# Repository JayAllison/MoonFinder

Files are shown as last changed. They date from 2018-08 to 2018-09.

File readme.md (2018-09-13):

Can I aim a telescope with a Raspberry Pi, some stepper motors, and some open-source software? Let's try!

Can I use **ALL** of the GPIO pins or a Raspberry Pi? Let's try!

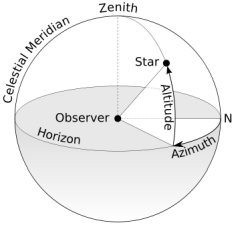
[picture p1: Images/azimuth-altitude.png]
Azimuth & Altitude
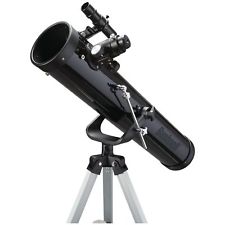
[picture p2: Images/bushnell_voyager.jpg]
 

### Equipment:

* Bushnell Voyager basic telescope (700mm x 76mm)
    * Probably need a mock-up, too - make it from 4" PVC?
* Raspberry Pi (I have both a Zero W and a 3B+, so I need to determine how much horsepower this application needs)
    * I also have protoboards to fit the GPIO of both
* 28BYJ-48 stepper motors and LN2003 drivers (I think I only need two, but I ordered [this five-pack](https://smile.amazon.com/gp/product/B015RQ97W8/) from Amazon)
* LSM303 digital compass (I ordered [this dev board](https://www.adafruit.com/product/1120) from Adafruit)
* Display (I ordered [this TFT display](https://smile.amazon.com/gp/product/B07B4BDWCL/) from Amazon)
    * I can always fall back to [this OLED display](https://smile.amazon.com/gp/product/B00O2LLT30/) if needed
* Limit switches (I ordered [this ten-pack](https://smile.amazon.com/gp/product/B00MFRMFS6/) from Amazon)
* 3/4" fender washers to use as weights (got two 25-packs at Home Depot)
* ~~Telephone handset jacks and cables for connecting motors to control board (ordered from Amazon)~~
* A two-way level (I ordered [this one](https://smile.amazon.com/gp/product/B000EDSSDO/) from Amazon)
* Buttons for user input (I ordered [this pack](https://smile.amazon.com/gp/product/B07CGCPGPT/) from Amazon)
* GPS (I ordered [this unit](https://smile.amazon.com/gp/product/B01H5FNA4K/) from Amazon)

### Source Code:

* My repository: https://github.com/JayAllison/MoonFinder

### Tools:

* Fritzing: http://fritzing.org/home/

### References:

* Python Raspberry Pi GPIO Wrapper Library: https://gpiozero.readthedocs.io/
* Raspberry Pi GPIO Pinout: https://pinout.xyz/
* Stepper motor control with RPi: https://tutorials-raspberrypi.com/how-to-control-a-stepper-motor-with-raspberry-pi-and-l293d-uln2003a/
    * But, my BlindsBot project ended up being a better reference for the step sequence
* LSM303 reading with RPi: https://github.com/adafruit/Adafruit_Python_LSM303/tree/master/examples
* ST7735 Display Library: https://github.com/cskau/Python_ST7735
    * I got the cheap Amazon display I purchased working with the examples using the connections listed below
    * The examples are written for a 160x128 display, this one is 128x128
* Python Image Library fork (pillow): https://pillow.readthedocs.io/en/5.2.x/
* U-Blox U-Center, Windows software for GPS module: https://www.u-blox.com/en/product/u-center-windows
* Serial Port driver: https://pythonhosted.org/pyserial/
* NMEA sentence information: http://aprs.gids.nl/nmea/
* RPi serial port info, per model: https://www.raspberrypi.org/documentation/configuration/uart.md
* gpsd, gpsmon: https://www.rs-online.com/designspark/add-gps-time-and-location-to-a-raspberry-pi-project
    * don't set gpsd to start up automatically or it will monopolize the serial port
* Astronomical positioning library: http://rhodesmill.org/pyephem/
* Python version of World Magnetic Model (offline): https://pypi.org/project/geomag/
* OpenSCAD (parametric 3D modeling): http://www.openscad.org/cheatsheet/

### 3D Models:

* need to design a pan-and-tilt mount for the telescope
* Do I need a counter-balance?
* Do I want to gear down the movement? or use worm gears instead?
* Can I do something kind of like this "Dobsonian" telescope?

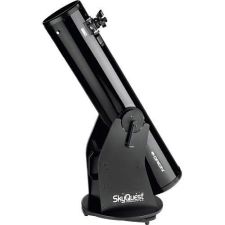
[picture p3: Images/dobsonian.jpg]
Dobsonian Telescope


### Basic Approach:

* User sets up telescope and verifies that the base is level
* Use compass to orient rotation (azimuth) of telescope to true North
* Use limit switch to orient angle (altitude) of telescope to horizontal
* Use library to calculate apparent position (azimuth, altitude) of desired celestial object
* Use stepper motors to aim telescope to that position
* Use stepper motors to either:
    * hold position
    * track object

### Remaining questions:

* How will the user specify the lat/lon location and altitude?
* How will the user select the celestial object?
* Will all of the libraries work offline, or will an internet connection be required?
* How to determine true north vs magnetic north, based on location?
* How to convert "apparent position" (azimuth, altitude) to pan and tilt rotations?
* How to implement tracking? How smooth do I want it to be?

### Hardware Ideas:

* I2C OLED screen or something similar
* Buttons for inputs (D Pad, 5 button style, etc)?
* Button for screen brightness?

### Software Ideas:

Display a list of known celestial objects that are currently visible?

### Raspberry Pi Setup Tasks:

*These are my standard steps for setting up a secure, headless Raspberry Pi*

- [x] Install Raspbian on RPi0W, add to WiFi, install updates
- [x] Change RPi hostname
- [x] Change locale via raspi-config? No, the new Raspbian setup took care of this.
- [x] Change keyboard layout via raspi-config? Yes, the new Raspbian setup did not take care of this.
- [x] Change timezone via raspi-config? No, the new Raspbian setup took care of this.
- [x] Enable SSH via raspi-config
- [x] Set up key-based SSH authentication
    * http://raspi.tv/2012/how-to-set-up-keys-and-disable-password-login-for-ssh-on-your-raspberry-pi
    * create sshd banner
- [x] Set up IP address emailing (had to use nano -u to remove dos line endings after I scp'd the file over from my PC)
    * https://gist.github.com/Morrolan/2987424#file-check_ip-py 
- [x] Install git? No, it was already installed. (Don't forget to set name and email address, though.)
- [x] Install screen
- [x] Install ipython
- [x] Modify /etc/nanorc to my liking
- [x] Set up RPi to boot w/o GUI via raspi-config
- [x] Set up RPi /etc/wpa_supplicant/wpa_supplicant.conf with WiFi credentials for home & work

### TFT Display Connections:

Display|Raspberry Pi
---|---
5V|any RPi 5V
GND|any RPi GND
GND|NC
NC|NC
NC|NC
LED|I connected this to RPi 3.3V
SCL|RPi SCLK
SDA|RPi MOSI
RS|GPIO 24 (per the example)
RST|GPIO 25 (per the example)
CS|RPi CE0

### Raspberry Pi Header Pin Allocation:

Usage|Pin|Name| |Name|Pin|Usage
----|---|---|---|---|---|---
X|_1_|**3.3V**| |**5V**|2|X
COMPASS|_3_|**I2C SDA (GPIO2)**| |**5V**|_4_|X
COMPASS|_5_|**I2C SCL (GPIO3)**| |**GND**|_6_|X
ERROR_LED|_7_|**GPIO4**| |**(GPIO14) TXD**|_8_|GPS
X|_9_|**GND**| |**(GPIO15) RXD**|_10_|GPS
MOTOR 1|_11_|**GPIO17**| |**(GPIO18) PWM0**|_12_|DISPLAY?
MOTOR 1|_13_|**GPIO27**| |**GND**|_14_|X
MOTOR 1|_15_|**GPIO22**| |**GPIO23**|_16_|MOTOR 1
X|_17_|**3.3V**| |**GPIO24**|_18_|DISPLAY
DISPLAY|_19_|**SPI MOSI (GPIO10)**| |**GND**|_20_|X
DISPLAY|_21_|**SPI MISO (GPIO9)**| |**GPIO25**|_22_|DISPLAY
DISPLAY|_23_|**SPI CLK (GPIO11)**| |**(GPIO8) SPI CE0**|_24_|DISPLAY
X|_25_|G**ND**| |**(GPIO7) SPI CE1**|_26_|SW 1
RESERVED|_27_|**ID_SD**| |**ID_SC**|_28_|RESERVED
MOTOR 2|_29_|**GPIO5**| |**GND**|_30_|X
MOTOR 2|_31_|**GPIO6**| |**GPIO12**|_32_|SW 2
LIMIT SWITCH|_33_|**PWM1 (GPIO13)**| |**GND**|_34_|X
MOTOR 2|_35_|**GPIO19**| |**GPIO16**|_36_|SW 3
MOTOR 2|_37_|**GPIO26**| |**GPIO20**|_38_|SW 4
X|_39_|**GND**| |**GPIO21**|_40_|SW 5

### Wiring to Handset:

* Using two stranded Ethernet cables

Wire|Cable A
---|---
1|5V
2|Display SPI MOSI
3|Display SPI MISO
4|Display SPI CLK
5|Display SPI CS
6|Display RS
7|Display RST
8|Display Backlight PWM

Wire|Cable B
---|---
1|3.3V
2|SW 1
3|SW 2
4|SW 3
5|SW 4
6|SW 5
7|ERROR LED
8|N/C

### Project Tasks:

- [x] Create ssh key for Bitbucket
- [x] Check out moonfinder repository onto RPi
- [x] Write pyephem example to show myself I can do it
- [x] Write stepper example to show myself I can do it
- [x] Enable I2C via raspi-config
- [x] Write compass example to show myself I can do it
- [x] Enable SPI via raspi-config
- [x] Write display example to show myself I can do it
- [x] Disable serial console, enable serial hardware via raspi-config, then reboot
- [x] Write GPS example to show myself I can do it
- [x] Install gpsd & gpsmon (only run gpsd on boot if you want to lose control of serial0!)
- [ ] Work on prototype of pan & tilt bracket
- [x] Build handset prototype
- [x] Design menuing software
- [ ] *Task TBD*
- [ ] *Task TBD*
- [ ] *Task TBD*
- [ ] *Task TBD*
- [ ] *Task TBD*
- [ ] *Task TBD*
- [ ] *Task TBD*
- [ ] Put it all together and try it out!

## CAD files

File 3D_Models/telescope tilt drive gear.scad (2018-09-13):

// Lay out the gears that I am going to use for the telescope mount

// the gear library I'm using
use <parametric_involute_gear_v5.0.scad>;

// my explicit gear parameters
number_of_teeth = 20;
pitch_diameter = 30;
pressure_angle = 30;
border_width = 5;
gear_thickness = 8;
border_thickness = gear_thickness;
hub_thickness = 13;
hub_diameter = 12;
circles = 0;

// my derived gear parameters
diametral_pitch = number_of_teeth / pitch_diameter;
echo(str("Diametral Pitch = ", diametral_pitch));
rim_thickness = border_thickness;
rim_width = border_width;

// gear parameters I'm not using
clearance = 0;
bore_diameter = 0;
backlash = 0;

// assemble the big gear - remember that its diametral pitch must match the mating gear
difference() {
    // lay out the basic gear
    gear(
        number_of_teeth=number_of_teeth,
        diametral_pitch=diametral_pitch,
        pressure_angle=pressure_angle,
        clearance=clearance,
        gear_thickness=gear_thickness,
        rim_thickness=rim_thickness,
        rim_width=rim_width,
        hub_thickness=hub_thickness,
        hub_diameter=hub_diameter,
        bore_diameter=bore_diameter,
        circles=circles,
        backlash=backlash
    );
    // create the axis type that I expect
    cube([5, 3, hub_thickness*2], center=true);
}

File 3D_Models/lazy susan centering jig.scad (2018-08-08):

// create a jig that fits in the center of the lazy susan bearing and aligns the bearing with the pin hole

hole_diameter = 33;
hole_height = 8;

pin_diameter = 3;
pin_height = 5;

union() {
    cylinder(h=hole_height, d=hole_diameter, center=false, $fn=256);
    translate([0,0,hole_height])
        cylinder(h=pin_height, d=pin_diameter, center=false, $fn=256);
}

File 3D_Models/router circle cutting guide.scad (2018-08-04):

// a custom jig for my Rigid router to cut a circle of the specified diameter
// this jig connects into the attachment rod holes that are built into my router's base

// specified parameter - how big of a circle do I want to cut: 8" ~= 203 mm
cut_circle_diameter = 205;

// specified parameter - what size bit am I using: 3/8" ~= 9.5 mm
bit_diameter = 10;

// measurements of my router
rod_depth = 20;
rod_width = 5;
rod_spread = 60;
bit_to_rod_bar_spacing = 65;

// design measurements for the jig
pin_diameter = 4;
disc_height = 18;
shaft_width = 10;
stiffener_height = 3;
stiffener_width = 0.4*3;

// calculated parameters
disc_diameter = pin_diameter*3;
shaft_length = cut_circle_diameter/2 + bit_diameter/2 - bit_to_rod_bar_spacing;
rod_spread_bar_length = rod_spread + rod_width;
shaft_height = shaft_width/2;

// put it all together
union() {
    difference() {
        union() {
            // create the pivot disc
            cylinder(h=disc_height, d=disc_diameter, center=true, $fn=256);
            // attach the extension shaft
            translate([-shaft_length, -shaft_width/2, -disc_height/2])
                cube(size=[shaft_length, shaft_width, shaft_height]);
            // add a stiffening spine to the extension shaft
            translate([-shaft_length, -stiffener_width/2, -disc_height/2+shaft_height])
                cube(size=[shaft_length, stiffener_width, stiffener_height]);
        }
        // punch the pin hole through the pivot disc
        cylinder(h=disc_height*2, d=pin_diameter, center=true, $fn=256);
    }
    // attach the rod spread bar to the shaft
    translate([-shaft_length, -rod_spread_bar_length/2, -disc_height/2]) {
        cube(size=[shaft_width, rod_spread_bar_length, shaft_height]);
    }
    // add a stiffening spine to the rod spread bar
    translate([-shaft_length+shaft_width/2-stiffener_width/2, -rod_spread_bar_length/2, -disc_height/2+shaft_height]) {
        cube(size=[stiffener_width, rod_spread_bar_length, stiffener_height]);
    }
    // attach first rod
    translate([-shaft_length-rod_depth, rod_spread_bar_length/2-rod_width, -disc_height/2])
        cube(size=[rod_depth, rod_width, rod_width]);
    // attach second rod
    translate([-shaft_length-rod_depth, -rod_spread_bar_length/2, -disc_height/2])
        cube(size=[rod_depth, rod_width, rod_width]);
}

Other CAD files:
3D_Models/parametric_involute_gear_v5.0.scad
3D_Models/telescope bracket gear.scad
3D_Models/telescope bracket.scad
3D_Models/telescope height adjuster foot.scad
3D_Models/telescope height adjuster knob.scad
3D_Models/telescope mount.scad
3D_Models/telescope weights bracket.scad

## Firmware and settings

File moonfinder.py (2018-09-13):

import atexit
import datetime
from gpiozero import LED
from lcd_display import lcd_display
import logging
from UserInterface import UserInterface
from Menu.menu_layout import top_menu
from PIL import Image
import signal
import syslog
import traceback

_PRINT_INSTEAD_OF_SYSLOG = False
_LOG_LEVEL = logging.WARNING

_ERROR_LED = 4

_UP_BUTTON = 7
_CENTER_BUTTON = 12
_DOWN_BUTTON = 16
_LEFT_BUTTON = 20
_RIGHT_BUTTON = 21

_error_led = None
_ui = None


def _log(message):

    if _PRINT_INSTEAD_OF_SYSLOG:
        print (str(datetime.datetime.now()) + " INFO: " + message)
    else:
        syslog.syslog(syslog.LOG_INFO, message)


def _log_error(message):

    if _PRINT_INSTEAD_OF_SYSLOG:
        print (str(datetime.datetime.now()) + " ERROR: " + message)
    else:
        syslog.syslog(syslog.LOG_ERR, message)


def _log_exception(message):

    if _PRINT_INSTEAD_OF_SYSLOG:
        print (str(datetime.datetime.now()) + " EXCEPTION: " + message)
    else:
        syslog.syslog(syslog.LOG_CRIT, message)
        syslog.syslog(syslog.LOG_CRIT, traceback.format_exc())


def start():
    logging.basicConfig(level=_LOG_LEVEL,
                        format='%(asctime)s %(levelname)s %(name)s %(message)s',
                        datefmt='%Y/%m/%d %I:%M:%S%p')

    global error_led
    error_led = LED(_ERROR_LED)
    error_led.off()

    logo = Image.open("Images/moon-icon.jpg")
    lcd_display.display(logo)

    # TODO: init the GPS
    # TODO: init the compass
    # TODO: zero out the azimuth using the compass
    # TODO: zero out the altitude using the limit switch

    # TODO: build a list of objects that are currently visible, and add them to the menu

    # initialize the user-interface state machine
    global _ui
    _ui = UserInterface("Moon Finder", lcd_display, top_menu, error_led,
                        _UP_BUTTON, _CENTER_BUTTON, _DOWN_BUTTON, _LEFT_BUTTON, _RIGHT_BUTTON)


# noinspection PyUnusedLocal
def stop(signum, frame):

    _log("SIGNAL received - stopping...")


def run():

    # initialize things
    start()

    # this is blocking - will not return
    _ui.run()


def on_exit():

    if error_led:
        error_led.on()
    _log("--- MoonFinder exiting ---")


if __name__ == "__main__":
    _log("--- MoonFinder starting ---")
    atexit.register(on_exit)
    signal.signal(signal.SIGINT, stop)
    signal.signal(signal.SIGTERM, stop)
    run()

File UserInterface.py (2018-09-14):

# a class that defines the user interface state machine for the MoonFinder application
# this class drives the LCD display and the menu system

from gpiozero import Button
from Menu.MenuElement import MenuElement
from PIL import ImageFont
from signal import pause

FONT_SIZE = 16
LEFT_MARGIN = 10
TOP_MARGIN = 10
TITLE_SPACING = 5
LINE_SPACING = 16
MENU_ITEM_MAX_CHARACTERS = 13
MENU_COLOR = (255,255,255)
TITLE_COLOR = (128, 128, 128)
SELECTED_COLOR = (255, 255, 0)

class UserInterface(object):

    def __init__(self,
                 title,
                 display,
                 top_menu,
                 error_led,
                 top_button_gpio,
                 center_button_gpio,
                 bottom_button_gpio,
                 left_button_gpio,
                 right_button_gpio):

        self.title = title
        self.display = display
        self.current_menu = top_menu
        self.selected = 0

        self.error_led = error_led

        self.top_button = Button(top_button_gpio)
        self.center_button = Button(center_button_gpio)
        self.bottom_button = Button(bottom_button_gpio)
        self.left_button = Button(left_button_gpio)
        self.right_button = Button(right_button_gpio)

        self.font = ImageFont.truetype("Fonts/Perfect DOS VGA 437 Win.ttf", FONT_SIZE)
        self.menu_color = MENU_COLOR
        self.title_color = TITLE_COLOR
        self.selected_color = SELECTED_COLOR

    def run(self):
        self.top_button.when_pressed = self.top_pressed
        self.center_button.when_pressed = self.center_pressed
        self.bottom_button.when_pressed = self.bottom_pressed
        self.left_button.when_pressed = self.left_pressed
        self.right_button.when_pressed = self.right_pressed

        # show the menu to the user
        self.show_menu()

        # now wait for the user's actions
        pause()

    def show_menu(self):
        # display is 128x128 - our working area is that less the margins and the title
        # each line of 16-pt font takes 10 pixels of space plus some separation
        # we can really only fit in 6 menu choices
        # TODO: scrolling a longer menu is not implemented

        self.display.clear((0, 0, 0))
        canvas = self.display.draw()
        x = LEFT_MARGIN
        y = TOP_MARGIN
        canvas.text((x, y), self.title, font=self.font, fill=self.title_color)
        y += TITLE_SPACING

        count = 0
        for item in self.current_menu.choices:
            y += LINE_SPACING
            color = self.selected_color if count == self.selected else self.menu_color
            title = item.title[:MENU_ITEM_MAX_CHARACTERS]
            if item.type == MenuElement.MENU:
                title = item.title[:MENU_ITEM_MAX_CHARACTERS-2] + " >"
            canvas.text((x, y), title, font=self.font, fill=color)
            count += 1

        self.display.display()

    # navigate down the menu
    def top_pressed(self):
        self.selected = self.selected - 1
        if self.selected < 0:
            self.selected = 0
        self.show_menu()

    # activate the current menu item
    def center_pressed(self):
        if self.current_menu.choices[self.selected].type == MenuElement.MENU:
            self.current_menu = self.current_menu.choices[self.selected]
            self.selected = 0
            self.show_menu()
        # TODO: activate the action...

    # navigate up the menu
    def bottom_pressed(self):
        self.selected = self.selected + 1
        if self.selected >= len(self.current_menu.choices):
            self.selected = len(self.current_menu.choices) - 1
        self.show_menu()

    # back out a level on the menu
    def left_pressed(self):
        if self.current_menu.parent:
            self.selected = 0
            count = -1
            for item in self.current_menu.parent.choices:
                count += 1
                if item == self.current_menu:
                    self.selected = count
                    break
            self.current_menu = self.current_menu.parent
            self.show_menu()

    # do what???
    def right_pressed(self):
        self.show_menu()

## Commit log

2018-07-19 Adding example of using gpiozero to drive stepper motor
2018-07-19 Updating stepper example after running on RPi - my stepper pattern from BlindsBot worked better than the stepper pattern I found online
2018-07-19 Stepper example clean-up
2018-07-23 Sample ephem script to generate a list of visible objects
2018-07-23 first attempt at 3D bracket to hold telescope
    [telescope bracket.scad]
2018-07-23 I wish OpenSCAD would auto-save!
    [telescope bracket.scad]
2018-07-24 Adjustments to basic bracket after printing first prototype
    [telescope bracket.scad]
2018-07-24 Fixed display example after running on actual hardware
    [display_example.py]
2018-07-26 The GPS position now prints to the screen clearly
2018-07-26 Tweaks to display example, fix PEP errors, etc.
    [display_example.py]
2018-07-31 Updated telescope bracket to have mount points, created a simple mount for the bracket, and developed a weight bracket that can hold 24 3/4" fender washers.
    [telescope bracket.scad, telescope mount.scad, telescope weights bracket.scad]
2018-08-04 Custom jig for my router's plunge base to cut an 8" hole if using a 3/8" bit
    [router circle cutting guide.scad]
2018-08-08 CAD design updates for assembling the telescope base
    [lazy susan centering jig.scad, telescope height adjuster foot.scad, telescope height adjuster knob.scad]
2018-09-13 CAD design updates for telescope-tilt gears
    [parametric_involute_gear_v5.0.scad, telescope bracket gear.scad, telescope tilt drive gear.scad]
2018-09-13 Reorganizing project into directories
    [lazy susan centering jig.scad, parametric_involute_gear_v5.0.scad, router circle cutting guide.scad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]
2018-09-13 Reorganizing project into directories (take 2)
    [lazy susan centering jig.scad, parametric_involute_gear_v5.0.scad, router circle cutting guide.scad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]
2018-09-13 Button example (now that handheld controller has been built)
2018-09-13 Modified button example (why is it so slow???)
2018-09-13 tweaked button script - it's fast enough now, btw
2018-09-13 Corrected font path based on new folder organization
    [display_example.py]
2018-09-13 Fixed basic UI exercise
    [UserInterface.py]
